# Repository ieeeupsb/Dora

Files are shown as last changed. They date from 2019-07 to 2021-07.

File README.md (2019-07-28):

View this project on [CADLAB.io](https://cadlab.io/project/1889). 

# Rasbot

## What is it?
This is a small differential terrestrial robot with all the sensors one can fit.
Its purpose is to have all the sensors and interfaces one can imagine so it can be used for research in various topics as well as different competitions.

Since its goal is to be resourceful in terms of sensing and actuating capabilities the design has expandability in mind. Therefore, there are a lot of exposed pins for modular expansions to the robot.

### Getting Support
There is extensive documentation on the Wiki page here on GitHub that covers the robot's design (hardware and software) as well as how to use this robot.

If you are a user of this robot and something is not working on your side please help us improve it. Open an issue here on GitHub!

### Contributing
Be it hardware or software, you can freely contribute to this project. Usually the Issues page here on GitHub has work that needs to be done. You are free to solve one yourself. Even if you are not familiar with hardware or software you can simply create new issues suggesting new things or changes/fixes to the current design.

This project is configured with CADLAB.io so visual differences of changes can be analysed.

If you are a contributor to this project keep in mind that pushing to the master branch is protected and can be only done by first creating a branch and then file a Pull Request which has to have at least two reviewers before it can be merged. This is meant to improve the quality of the project.

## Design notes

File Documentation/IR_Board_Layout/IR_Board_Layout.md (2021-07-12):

# Description

To do

# Size

To do

# To do

- [ ] Verify schematic
- [ ] Create basic layout figure
- [ ] Define board setup (track width, clearance, etc)
- [ ] Define board size
- [ ] Layout the board
- [ ] Check for possible issues with connections and sizes

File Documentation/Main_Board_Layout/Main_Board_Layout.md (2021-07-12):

# Description

## List of systems:
* Motors
  * Motor 1
  * Motor 2
  * Motor 3
  * Motor 4
  * Motor Encoders
* Power
  * 3.3V Buck
  * 5V Ultrasonic Buck
  * 5V RPi Buck
  * BMS
* MCU System
  * MCU
  * Power LED
  * Clock
  * EEPROM
  * Reset
  * Programming/Debugging
* IO System
  * RPi Headers
  * Expansion Headers
  * OLED
  * IMU
  * Buzzer
  * IR Array Module
  * RGB Leds
  * UltraSonic 1
  * UltraSonic 2
  * UltraSonic 3
  * UltraSonic 4

# Size

To do

# To do

- [ ] Verify schematic
- [ ] Create basic layout figure
- [ ] Define board setup (track width, clearance, etc)
- [ ] Define board size
- [ ] Layout the board
- [ ] Check for possible issues with connections and sizes

## Schematic
- [ ]  Jumpers SPI to IR board -> Add 100ohm (p.ex) resistance series to filter noise found on the connection wires (mainly in MISO, MOSI and CLK wires)
- [ ]  Check I2C1 and I2C2 resistors -> Normally 1-10k per device
- [ ]  Check bucks, mainly RPi 5v buck -> Vasco will check
- [ ]  Check dimensions of RPi to verify that it fits over the PCB
- [ ]  Check if IDC connector can handle 2.5A to RPi -> Vasco (Investigate the possibility of barrel jack RPi Power)

## Physical
- [ ]  Possibilities:
	* MicroRato: Dora Presentation (20cm×20cm  de  base  e  30cm  de altura)
		* Largura minima = Largura de motores + rodas
		* https://arxiv.org/pdf/1901.03638.pdf
	* Outro exemplo: 
		* https://developer.nvidia.com/embedded/diy-ai-race
		* https://www.myminifactory.com/object/3d-print-myrccar-1-10-mtc-chassis-rigid-axles-version-customizable-chassis-for-monster-crawler-or-scale-rc-car-79883	

# Some tips

## Layers
* Top layer -> Mixed
* In1 layer -> power plane (GND)
	*	Isolated GND planes for 3.3V, 5V and BAT with a small physical connection between them
* In2 layer -> power plane (VDD)
	* Isolated voltage planes
* Bot layer -> Mixed

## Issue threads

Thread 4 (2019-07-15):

Verify IR Matrix

G-Pereira, 2019-07-15:
Verify if the present IR Matrix schematic is correct.
The idea behind the current implementation is:
- One 9V rail powers each column completely to reduce components and power usage.
- Each column has its outputs multiplexed in order to read data row by row in parallel in order to reduce input pins to the number of rows.

However, this might not be optimal since 9V is too close to battery voltage and the battery can be lower than 9V during a normal discharge cycle. At the moment the plan is to use a buck-boost converter (acts as a buck while the battery is above 9V and as a boost while it's lower than that). Evaluate if it's needed to change this strategy.

G-Pereira, 2019-07-15:
Sadly there's no spice models for the CD4051B multiplexer

Closed 2019-07-22.

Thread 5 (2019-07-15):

Motor Driver

G-Pereira, 2019-07-15:
For the motors we already have (ask for the voltage rating) design the motor driver circuit and define its power draw at max output power.
It's useful to have a current limiting architecture here. There are several ways to do this, ask in Slack if you are lost.

Closed 2019-08-21.

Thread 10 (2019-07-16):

connect IMU system

G-Pereira, 2019-07-16:
Connect gyroscope and compass to the I2C bus and if needed set their configuration pins.

G-Pereira, 2019-08-05:
Sorry to change this even tho the schematic is already settled but BMX055 is the same as BNO055 without the ARM microcontroller built-in. This means changing to BMX055 gives access to raw sensor data and a considerably price drop.

Closed 2021-03-10.

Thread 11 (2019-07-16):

Design connection from Raspberry Pi to MCU

G-Pereira, 2019-07-16:
Maybe just one UART connection is needed but take some time to think what interfaces are useful and what the Raspberry could be able to do. Then, design a schematic for that

Closed 2019-09-09.

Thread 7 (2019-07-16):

Design RF Receiver

G-Pereira, 2019-07-16:
~~Design a RF Receiver decoder to read a RF433 module in order to design a remote control later on.
The idea is to expose a Dupont connector to plug in a receiver but it's necessary to deserialize the data that comes from it.
First 8 bits are address and the next 4 are data so in other to offload address verification the use of HT12D is highly recommended. The MCU would have to constantly read all RF signals and evaluate if it's our remote talking. This way the MCU receives from HT12D's VT pin (connected to an interruption enabled pin) a signal that our remote has sent data and then the data pins can be read in order to read the command sent through.~~

~~An NRF24 make the process esier, is more reliable, faster, supports longer distance and it's way cheaper. A more reputable brand (Nordic Semiconductor) manufactures them.
Design a connector for it. It uses SPI~~

Design a LoRa interface

Closed 2019-08-26.

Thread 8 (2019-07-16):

LCD Screen Menu Interface

G-Pereira, 2019-07-16:
In other to change robot's parameters or function and display battery status, design a connector for a SSD1306 LCD. Include a clickable rotary encoder in order to navigate menu. Plan the connections to the MCU.

Closed 2019-07-28.

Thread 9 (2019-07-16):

Read Motor Encoders

G-Pereira, 2019-07-16:
Our motors include two magnetic sensors to read motors rotation. Plan the connection of this 4 pins (2 for each motor). Evaluate if more than direct connection is possible. These pins if connected to an interrupt pin can generate a high rate of interrupt calls and that will require a high frequency clock MCU which can be avoided. Design a hardware solution for this.

Closed 2019-07-28.

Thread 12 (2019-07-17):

Ultrassonic Sensors connectors

G-Pereira, 2019-07-17:
Design a connection for sonars (dupont). Each one consists of 4 pins:
- Power (VCC and GND)
- Trig - Sensor input to begin reading process (Generic MCU I/O)
- Echo - sensor output signal (Generic MCU I/O)
There will be 4 of them

Closed 2019-07-28.

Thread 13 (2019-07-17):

Battery Level Sensor

G-Pereira, 2019-07-17:
Design hardware to read efficiently the battery status (there's ICs in the market for this).
Make sure the solution is appropriate for LiPo batteries.
Battery will be a LiPo 3C 11.1V

Sleepy105, 2019-07-22:
https://www.digikey.com/product-detail/en/texas-instruments/BQ76925PWR/296-29341-1-ND/2728027

JoaoGarrido, 2019-07-29:
Datasheet:
http://www.ti.com/lit/ds/symlink/bq76925.pdf
Application notes:
http://www.ti.com/lit/an/slua707/slua707.pdf

Some notes:
- LDO regulator from the IC will not power the MCU(what should i do with it?)
- Not sure how to do the battery temperature part

Closed 2021-03-10.

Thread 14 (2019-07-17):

Add debug interfaces (visual or audible)

G-Pereira, 2019-07-17:
Add 1 buzzer and 3 RGB LED to help debug applications and to show various status like battery's status.
Use PWM for both buzzer and RGB LEDs.
Add more if you find it useful

G-Pereira, 2019-07-22:
1K resistor fits both interfaces and minimizes power usage.

Closed 2019-07-28.

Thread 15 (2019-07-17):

Design Buck Converters

G-Pereira, 2019-07-17:
This should be only done at the end of the schematic where the circuit is well defined in terms of power draw.
From the time of this writing it is being planned to have various voltage levels. Use a Texas Instruments device for this since there's experience with these ICs.

Closed 2019-08-26.

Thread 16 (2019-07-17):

Early pick of MCU

G-Pereira, 2019-07-17:
At this stage pick a STM32 family of devices by looking at their top level features and pick one with a decent amount of pins to begin planning MCU connections. Don't waste time thinking on the number of I/O in detail.
On the final stages of development the MCU will be revised and sized.
Only make sure to set STM32 family on stone (this is important) in order to avoid wasting time.

Sleepy105, 2019-07-22:
STM32F4 family

Closed 2019-07-22.

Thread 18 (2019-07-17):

Design add-on connector

G-Pereira, 2019-07-17:
Design a connector for future improvements of the robot.
Be sure to expose everything it can be used. Don't forget to expose I2C and SPI bus even if that's in use because it can be added more devices to those buses.

Closed 2021-03-10.

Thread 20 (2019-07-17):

Design PCB

G-Pereira, 2019-07-17:
Layout components on the PCB. @G-Pereira will be definitively involved in this but be free to assign yourself also to this issue if you would like to help.

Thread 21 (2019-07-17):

Design CAD Model of Enclosure

G-Pereira, 2019-07-17:
Design an enclosure that fits a 100x100mm PCB. The fixings can be anywhere, just inform Electrical team where you plan to have screws or other types of fixings.

pedro-brands, 2019-07-17:
Portanto, eu vou fazer o design estrutural e o outro Pedro vai servir de consultor.

G-Pereira, 2019-07-18:
Ok, porreiro. nós vamos ter duas PCBs, uma mais junto ao chão com sensores de linha e outra principal. a ideia é fazer o robô o mais pequeno possivel e a PCB vai ter um máximo de 100x100mm (pode vir a ser mais pequena). Temos dois motores já no núcleo, as dimensões vão ser publicadas aqui #22 e por fim, temos de colocar vários LEDs (na verdade são sensores) a apontar para todas as direções (por volta de 12 LEDs) a uma altura razoável, por isso é preciso planear uma espécie de torre também. Tudo claro?

pedro-brands, 2019-07-18:
Muito bem, percebido! O luis já me tinha dado algumas indicações! Amanhã começo a fazer drafts de como pode ser o modelo e depois coloco aqui

G-Pereira, 2019-07-19:
Porreiro!

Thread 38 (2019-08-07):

Computer mouse sensor

G-Pereira, 2019-08-07:
Use an off-the-shelf computer mouse tracking sensor to improve the odometry of the robot. This should be designed as a plugin since it will be detached from the mainboard. This sensor, as you know, has to be really close to the ground almost dragging. Discuss with MCAD team if this is feasible.

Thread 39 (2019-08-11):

Add EEPROM

G-Pereira, 2019-08-11:
High performance STM32 MCU doesn't feature an EEPROM. This can be useful for configurations. Pick one EEPROM chip and design a circuit to connect it to the MCU

G-Pereira, 2019-08-12:
24LC256 was picked

Closed 2019-08-14.

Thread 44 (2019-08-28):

Design HouseKeeping circuit

G-Pereira, 2019-08-28:
Design a microcontroller circuit that is responsible for the safe functioning of the device that is responsible for safe shutdown of raspberry pi, power on/off power rails and subcircuits. This microcontroller will be alway connected to the battery so it should be a STM32L series to get power consumption of around 50uA. Because of this the external power switch will be a soft shutdown so a not so accessible (so people don't use it) power switch should be integrated because even with low current draw, after months the battery could be wasted.

G-Pereira, 2019-09-07:
Not really important

Closed 2019-09-07.

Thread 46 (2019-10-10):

Level Shifters Sonar

G-Pereira, 2019-10-10:
Sonar Echo pins need to be shifted to 3.3V logic with AO3400

morallito, 2019-10-19:
Implementado no branch BMS commit "3.3 - 5V level shifter sonar with 2n3904

morallito, 2019-10-19:
@G-Pereira confira se é isto que querias!

Closed 2019-10-25.

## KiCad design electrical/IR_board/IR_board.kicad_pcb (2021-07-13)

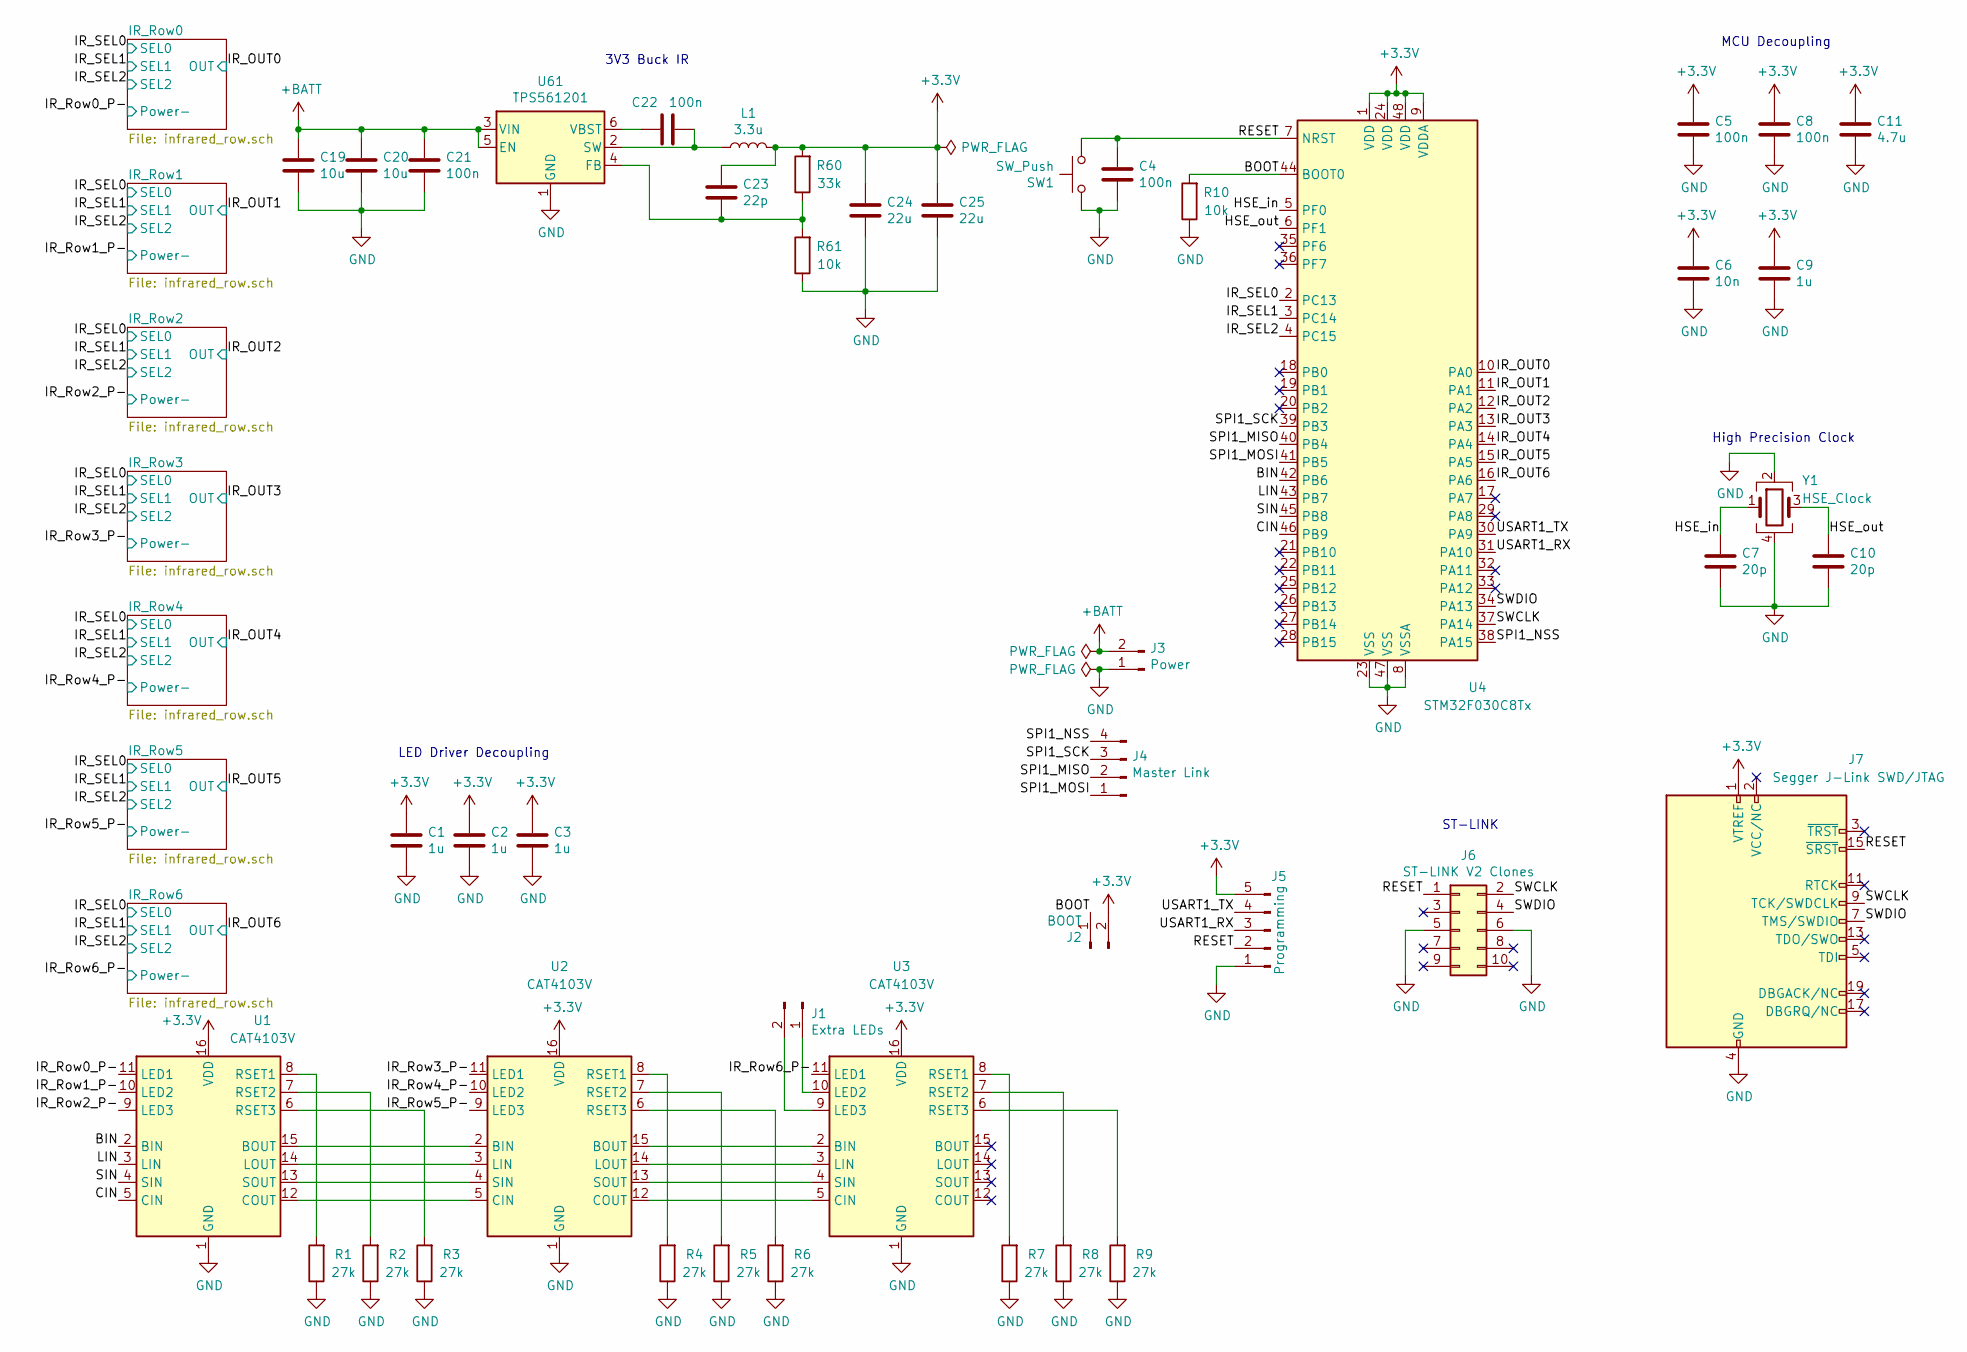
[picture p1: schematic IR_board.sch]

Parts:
C1, C2, C3, C9: 1u; C_0603_1608Metric
C4, C5, C8: 100n; C_0603_1608Metric
C6: 10n; C_0603_1608Metric
C7, C10: 20p; C_0603_1608Metric
C11: 4.7u; C_0603_1608Metric
C19, C20: 10u; C_1206_3216Metric
C21, C22: 100n; C_1206_3216Metric
C23: 22p; C_0603_1608Metric
C24, C25: 22u; C_0603_1608Metric
J1: Extra LEDs; PinHeader_1x02_P2.54mm_Horizontal
J2: BOOT; PinHeader_1x02_P2.54mm_Horizontal
J3: Power; JST_XH_S2B-XH-A-1_1x02_P2.50mm_Horizontal
J4: Master Link; JST_XH_S4B-XH-A-1_1x04_P2.50mm_Horizontal
J5: Programming; PinHeader_1x05_P2.54mm_Horizontal
J6: ST-LINK V2 Clones; IDC-Header_2x05_P2.54mm_Vertical
J7: Segger J-Link SWD/JTAG; IDC-Header_2x10_P2.54mm_Vertical
L1: 3.3u; L_Coilcraft_LPS4018
R1, R2, R3, R4, R5, R6, R7, R8, R9: 27k; R_0603_1608Metric
R10, R61: 10k; R_0603_1608Metric
R60: 33k; R_0603_1608Metric
SW1: SW_Push; SW_PUSH_6mm
U1, U2, U3: CAT4103V; SOIC-16_3.9x9.9mm_P1.27mm
U4: STM32F030C8Tx; LQFP-48_7x7mm_P0.5mm
U61: TPS561201; SOT-23-8
Y1: HSE_Clock; Crystal_SMD_5032-4Pin_5.0x3.2mm

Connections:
+3V3: C1.1, C2.1, C3.1, C5.1, C6.1, C8.1, C9.1, C11.1, C23.1, C24.1, C25.1, J2.2, J5.5, J7.1 (VTREF), L1.2, R60.2, U1.16 (VDD), U2.16 (VDD), U3.16 (VDD), U4.1 (VDD), U4.9 (VDDA), U4.24 (VDD), U4.48 (VDD); also elsewhere on the board
+BATT: C19.1, C20.1, C21.1, J3.2, U61.3 (VIN), U61.5 (EN); also elsewhere on the board
/BIN: U1.2 (BIN), U4.42 (PB6)
/BOOT: J2.1, R10.2, U4.44 (BOOT0)
/CIN: U1.5 (CIN), U4.46 (PB9)
/HSE_in: C7.1, U4.5 (PF0), Y1.1
/HSE_out: C10.1, U4.6 (PF1), Y1.3
/IR_OUT0: U4.10 (PA0); also elsewhere on the board
/IR_OUT1: U4.11 (PA1); also elsewhere on the board
/IR_OUT2: U4.12 (PA2); also elsewhere on the board
/IR_OUT3: U4.13 (PA3); also elsewhere on the board
/IR_OUT4: U4.14 (PA4); also elsewhere on the board
/IR_OUT5: U4.15 (PA5); also elsewhere on the board
/IR_OUT6: U4.16 (PA6); also elsewhere on the board
/IR_Row0_P-: U1.11 (LED1); also elsewhere on the board
/IR_Row1_P-: U1.10 (LED2); also elsewhere on the board
/IR_Row2_P-: U1.9 (LED3); also elsewhere on the board
/IR_Row3_P-: U2.11 (LED1); also elsewhere on the board
/IR_Row4_P-: U2.10 (LED2); also elsewhere on the board
/IR_Row5_P-: U2.9 (LED3); also elsewhere on the board
/IR_Row6_P-: U3.11 (LED1); also elsewhere on the board
/IR_SEL0: U4.2 (PC13); also elsewhere on the board
/IR_SEL1: U4.3 (PC14); also elsewhere on the board
/IR_SEL2: U4.4 (PC15); also elsewhere on the board
/LIN: U1.3 (LIN), U4.43 (PB7)
/RESET: C4.1, J5.2, J6.1, J7.15 (~SRST~), SW1.2, U4.7 (NRST)
/SIN: U1.4 (SIN), U4.45 (PB8)
/SPI1_MISO: J4.2, U4.40 (PB4)
/SPI1_MOSI: J4.1, U4.41 (PB5)
/SPI1_NSS: J4.4, U4.38 (PA15)
/SPI1_SCK: J4.3, U4.39 (PB3)
/SWCLK: J6.2, J7.9 (TCK/SWDCLK), U4.37 (PA14)
/SWDIO: J6.4, J7.7 (TMS/SWDIO), U4.34 (PA13)
/USART1_RX: J5.3, U4.31 (PA10)
/USART1_TX: J5.4, U4.30 (PA9)
GND: C1.2, C2.2, C3.2, C4.2, C5.2, C6.2, C7.2, C8.2, C9.2, C10.2, C11.2, C19.2, C20.2, C21.2, C24.2, C25.2, J3.1, J5.1, J6.5, J6.6, J7.4 (GND), J7.6 (GND), J7.8 (GND), J7.10 (GND), J7.12 (GND), J7.14 (GND), J7.16 (GND), J7.18 (GND), J7.20 (GND), R1.1, R2.1, R3.1, R4.1, R5.1, R6.1, R7.1, R8.1, R9.1, R10.1, R61.1, SW1.1, U1.1 (GND), U2.1 (GND), U3.1 (GND), U4.8 (VSSA), U4.23 (VSS), U4.47 (VSS), U61.1 (GND), Y1.2, Y1.4; also elsewhere on the board
unnamed: C22.1, U61.6 (VBST)
unnamed: C22.2, L1.1, U61.2 (SW)
unnamed: C23.2, R60.1, R61.2, U61.4 (FB)
unnamed: J1.1, U3.10 (LED2)
unnamed: J1.2, U3.9 (LED3)
unnamed: R1.2, U1.8 (RSET1)
unnamed: R2.2, U1.7 (RSET2)
unnamed: R3.2, U1.6 (RSET3)
unnamed: R4.2, U2.8 (RSET1)
unnamed: R5.2, U2.7 (RSET2)
unnamed: R6.2, U2.6 (RSET3)
unnamed: R7.2, U3.8 (RSET1)
unnamed: R8.2, U3.7 (RSET2)
unnamed: R9.2, U3.6 (RSET3)
unnamed: U1.12 (COUT), U2.5 (CIN)
unnamed: U1.13 (SOUT), U2.4 (SIN)
unnamed: U1.14 (LOUT), U2.3 (LIN)
unnamed: U1.15 (BOUT), U2.2 (BIN)
unnamed: U2.12 (COUT), U3.5 (CIN)
unnamed: U2.13 (SOUT), U3.4 (SIN)
unnamed: U2.14 (LOUT), U3.3 (LIN)
unnamed: U2.15 (BOUT), U3.2 (BIN)

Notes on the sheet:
LED Driver Decoupling
ST-LINK
High Precision Clock
MCU Decoupling
3V3 Buck IR

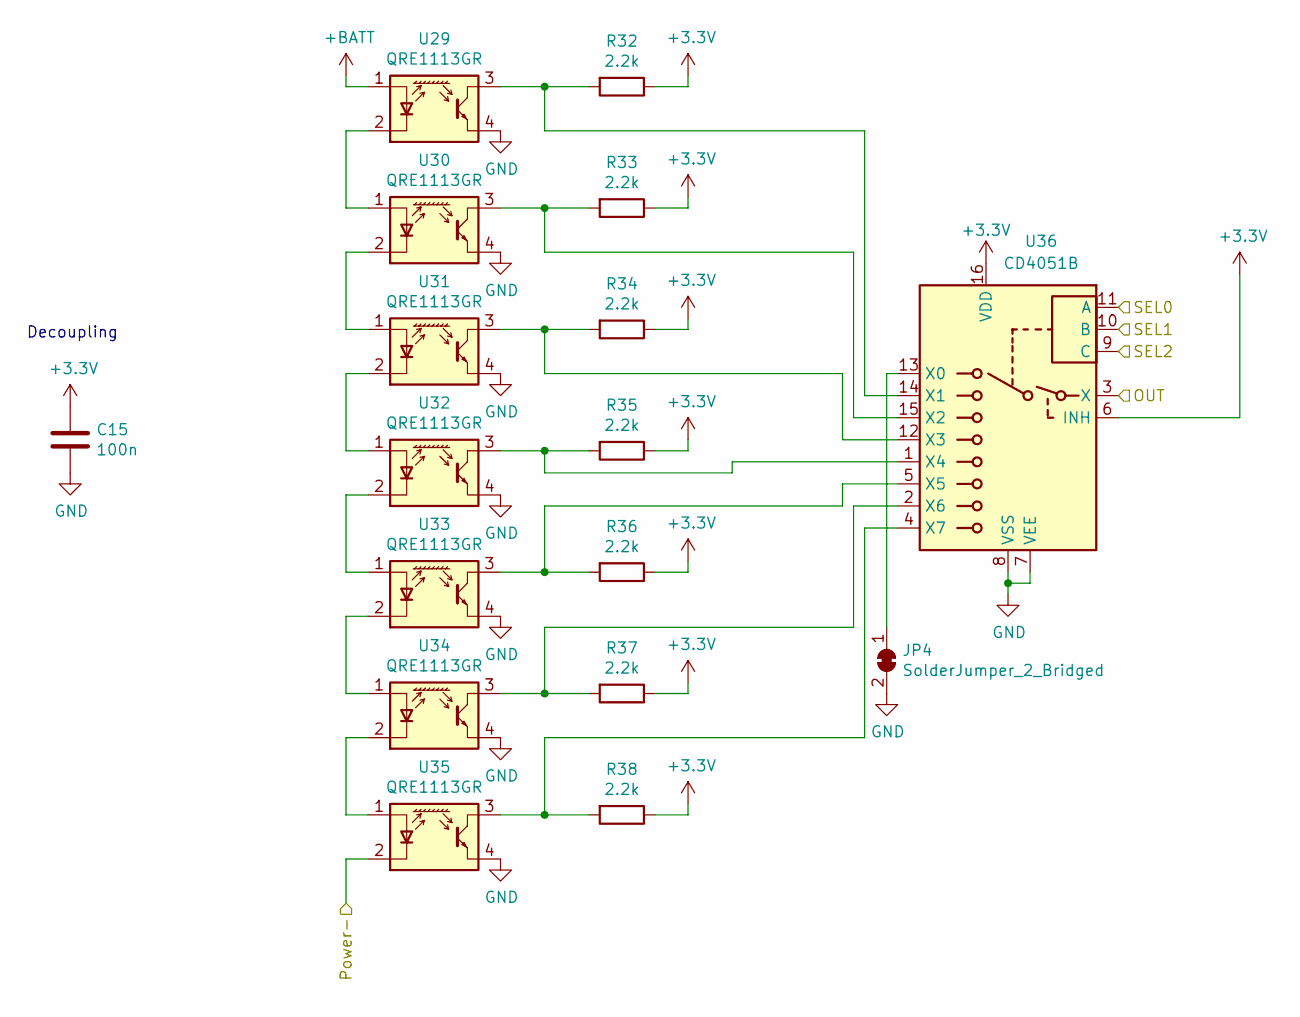
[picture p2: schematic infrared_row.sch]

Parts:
C17: 100n; C_0603_1608Metric
JP4: SolderJumper_2_Bridged; SolderJumper-2_P1.3mm_Bridged_Pad1.0x1.5mm
R46, R47, R48, R49, R50, R51, R52: 2.2k; R_0603_1608Metric
U45, U46, U47, U48, U49, U50, U51: QRE1113GR; OnSemi_CASE100CY
U52: CD4051B; SOP-16_4.55x10.3mm_P1.27mm

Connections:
+3V3: C17.1, R46.1, R47.1, R48.1, R49.1, R50.1, R51.1, R52.1, U52.6 (INH), U52.16 (VDD); also elsewhere on the board
+BATT: U45.1 (A); also elsewhere on the board
/IR_OUT6: U52.3 (X); also elsewhere on the board
/IR_Row6_P-: U51.2 (K); also elsewhere on the board
/IR_SEL0: U52.11 (A); also elsewhere on the board
/IR_SEL1: U52.10 (B); also elsewhere on the board
/IR_SEL2: U52.9 (C); also elsewhere on the board
GND: C17.2, JP4.2 (B), U45.4, U46.4, U47.4, U48.4, U49.4, U50.4, U51.4, U52.7 (VEE), U52.8 (VSS); also elsewhere on the board
unnamed: R46.2, U45.3, U52.14 (X1)
unnamed: R47.2, U46.3, U52.15 (X2)
unnamed: R48.2, U47.3, U52.12 (X3)
unnamed: R49.2, U48.3, U52.1 (X4)
unnamed: R50.2, U49.3, U52.5 (X5)
unnamed: R51.2, U50.3, U52.2 (X6)
unnamed: R52.2, U51.3, U52.4 (X7)
unnamed: U45.2 (K), U46.1 (A)
unnamed: U46.2 (K), U47.1 (A)
unnamed: U47.2 (K), U48.1 (A)
unnamed: U48.2 (K), U49.1 (A)
unnamed: U49.2 (K), U50.1 (A)
unnamed: U50.2 (K), U51.1 (A)

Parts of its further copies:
C12, C13, C14, C15, C16, C18: 100n; C_0603_1608Metric
JP1, JP2, JP3, JP5, JP6, JP7: SolderJumper_2_Bridged; SolderJumper-2_P1.3mm_Bridged_Pad1.0x1.5mm
R11, R12, R13, R14, R15, R16, R17, R18, R19, R20, R21, R22, R23, R24, R25, R26, R27, R28, R29, R30, R31, R32, R33, R34, R35, R36, R37, R38, R39, R40, R41, R42, R43, R44, R45, R53, R54, R55, R56, R57, R58, R59: 2.2k; R_0603_1608Metric
U5, U6, U7, U8, U9, U10, U11, U13, U14, U15, U16, U17, U18, U19, U21, U22, U23, U24, U25, U26, U27, U29, U30, U31, U32, U33, U34, U35, U37, U38, U39, U40, U41, U42, U43, U53, U54, U55, U56, U57, U58, U59: QRE1113GR; OnSemi_CASE100CY
U12, U20, U28, U36, U44, U60: CD4051B; SOP-16_4.55x10.3mm_P1.27mm

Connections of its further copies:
+3V3: C12.1, C13.1, C14.1, C15.1, C16.1, C18.1, R11.1, R12.1, R13.1, R14.1, R15.1, R16.1, R17.1, R18.1, R19.1, R20.1, R21.1, R22.1, R23.1, R24.1, R25.1, R26.1, R27.1, R28.1, R29.1, R30.1, R31.1, R32.1, R33.1, R34.1, R35.1, R36.1, R37.1, R38.1, R39.1, R40.1, R41.1, R42.1, R43.1, R44.1, R45.1, R53.1, R54.1, R55.1, R56.1, R57.1, R58.1, R59.1, U12.6 (INH), U12.16 (VDD), U20.6 (INH), U20.16 (VDD), U28.6 (INH), U28.16 (VDD), U36.6 (INH), U36.16 (VDD), U44.6 (INH), U44.16 (VDD), U60.6 (INH), U60.16 (VDD); also elsewhere on the board
+BATT: U5.1 (A), U13.1 (A), U21.1 (A), U29.1 (A), U37.1 (A), U53.1 (A); also elsewhere on the board
/IR_OUT0: U60.3 (X); also elsewhere on the board
/IR_OUT1: U12.3 (X); also elsewhere on the board
/IR_OUT2: U44.3 (X); also elsewhere on the board
/IR_OUT3: U20.3 (X); also elsewhere on the board
/IR_OUT4: U28.3 (X); also elsewhere on the board
/IR_OUT5: U36.3 (X); also elsewhere on the board
/IR_Row0_P-: U59.2 (K); also elsewhere on the board
/IR_Row1_P-: U11.2 (K); also elsewhere on the board
/IR_Row2_P-: U43.2 (K); also elsewhere on the board
/IR_Row3_P-: U19.2 (K); also elsewhere on the board
/IR_Row4_P-: U27.2 (K); also elsewhere on the board
/IR_Row5_P-: U35.2 (K); also elsewhere on the board
/IR_SEL0: U12.11 (A), U20.11 (A), U28.11 (A), U36.11 (A), U44.11 (A), U60.11 (A); also elsewhere on the board
/IR_SEL1: U12.10 (B), U20.10 (B), U28.10 (B), U36.10 (B), U44.10 (B), U60.10 (B); also elsewhere on the board
/IR_SEL2: U12.9 (C), U20.9 (C), U28.9 (C), U36.9 (C), U44.9 (C), U60.9 (C); also elsewhere on the board
GND: C12.2, C13.2, C14.2, C15.2, C16.2, C18.2, JP1.2 (B), JP2.2 (B), JP3.2 (B), JP5.2 (B), JP6.2 (B), JP7.2 (B), U5.4, U6.4, U7.4, U8.4, U9.4, U10.4, U11.4, U12.7 (VEE), U12.8 (VSS), U13.4, U14.4, U15.4, U16.4, U17.4, U18.4, U19.4, U20.7 (VEE), U20.8 (VSS), U21.4, U22.4, U23.4, U24.4, U25.4, U26.4, U27.4, U28.7 (VEE), U28.8 (VSS), U29.4, U30.4, U31.4, U32.4, U33.4, U34.4, U35.4, U36.7 (VEE), U36.8 (VSS), U37.4, U38.4, U39.4, U40.4, U41.4, U42.4, U43.4, U44.7 (VEE), U44.8 (VSS), U53.4, U54.4, U55.4, U56.4, U57.4, U58.4, U59.4, U60.7 (VEE), U60.8 (VSS); also elsewhere on the board
unnamed: JP1.1 (A), U12.13 (X0)
unnamed: JP2.1 (A), U20.13 (X0)
unnamed: JP3.1 (A), U28.13 (X0)
unnamed: JP5.1 (A), U44.13 (X0)
unnamed: JP7.1 (A), U60.13 (X0)
unnamed: R11.2, U5.3, U12.14 (X1)
unnamed: R12.2, U6.3, U12.15 (X2)
unnamed: R13.2, U7.3, U12.12 (X3)
unnamed: R14.2, U8.3, U12.1 (X4)
unnamed: R15.2, U9.3, U12.5 (X5)
unnamed: R16.2, U10.3, U12.2 (X6)
unnamed: R17.2, U11.3, U12.4 (X7)
unnamed: R18.2, U13.3, U20.14 (X1)
unnamed: R19.2, U14.3, U20.15 (X2)
unnamed: R20.2, U15.3, U20.12 (X3)
unnamed: R21.2, U16.3, U20.1 (X4)
unnamed: R22.2, U17.3, U20.5 (X5)
unnamed: R23.2, U18.3, U20.2 (X6)
unnamed: R24.2, U19.3, U20.4 (X7)
unnamed: R25.2, U21.3, U28.14 (X1)
unnamed: R26.2, U22.3, U28.15 (X2)
unnamed: R27.2, U23.3, U28.12 (X3)
unnamed: R28.2, U24.3, U28.1 (X4)
unnamed: R29.2, U25.3, U28.5 (X5)
unnamed: R30.2, U26.3, U28.2 (X6)
unnamed: R31.2, U27.3, U28.4 (X7)
unnamed: R32.2, U29.3, U36.14 (X1)
unnamed: R33.2, U30.3, U36.15 (X2)
unnamed: R34.2, U31.3, U36.12 (X3)
unnamed: R35.2, U32.3, U36.1 (X4)
unnamed: R36.2, U33.3, U36.5 (X5)
unnamed: R37.2, U34.3, U36.2 (X6)
unnamed: R38.2, U35.3, U36.4 (X7)
unnamed: R39.2, U37.3, U44.14 (X1)
unnamed: R40.2, U38.3, U44.15 (X2)
unnamed: R41.2, U39.3, U44.12 (X3)
unnamed: R42.2, U40.3, U44.1 (X4)
unnamed: R43.2, U41.3, U44.5 (X5)
unnamed: R44.2, U42.3, U44.2 (X6)
unnamed: R45.2, U43.3, U44.4 (X7)
unnamed: R53.2, U53.3, U60.14 (X1)
unnamed: R54.2, U54.3, U60.15 (X2)
unnamed: R55.2, U55.3, U60.12 (X3)
unnamed: R56.2, U56.3, U60.1 (X4)
unnamed: R57.2, U57.3, U60.5 (X5)
unnamed: R58.2, U58.3, U60.2 (X6)
unnamed: R59.2, U59.3, U60.4 (X7)
unnamed: U5.2 (K), U6.1 (A)
unnamed: U6.2 (K), U7.1 (A)
unnamed: U7.2 (K), U8.1 (A)
unnamed: U8.2 (K), U9.1 (A)
unnamed: U9.2 (K), U10.1 (A)
unnamed: U10.2 (K), U11.1 (A)
unnamed: U13.2 (K), U14.1 (A)
unnamed: U14.2 (K), U15.1 (A)
unnamed: U15.2 (K), U16.1 (A)
unnamed: U16.2 (K), U17.1 (A)
unnamed: U17.2 (K), U18.1 (A)
unnamed: U18.2 (K), U19.1 (A)
unnamed: U21.2 (K), U22.1 (A)
unnamed: U22.2 (K), U23.1 (A)
unnamed: U23.2 (K), U24.1 (A)
unnamed: U24.2 (K), U25.1 (A)
unnamed: U25.2 (K), U26.1 (A)
unnamed: U26.2 (K), U27.1 (A)
unnamed: U29.2 (K), U30.1 (A)
unnamed: U30.2 (K), U31.1 (A)
unnamed: U31.2 (K), U32.1 (A)
unnamed: U32.2 (K), U33.1 (A)
unnamed: U33.2 (K), U34.1 (A)
unnamed: U34.2 (K), U35.1 (A)
unnamed: U37.2 (K), U38.1 (A)
unnamed: U38.2 (K), U39.1 (A)
unnamed: U39.2 (K), U40.1 (A)
unnamed: U40.2 (K), U41.1 (A)
unnamed: U41.2 (K), U42.1 (A)
unnamed: U42.2 (K), U43.1 (A)
unnamed: U53.2 (K), U54.1 (A)
unnamed: U54.2 (K), U55.1 (A)
unnamed: U55.2 (K), U56.1 (A)
unnamed: U56.2 (K), U57.1 (A)
unnamed: U57.2 (K), U58.1 (A)
unnamed: U58.2 (K), U59.1 (A)

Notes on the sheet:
Decoupling

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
Board: 2 copper layers, 164 parts (0 on the bottom side), 156 nets, no tracks yet.

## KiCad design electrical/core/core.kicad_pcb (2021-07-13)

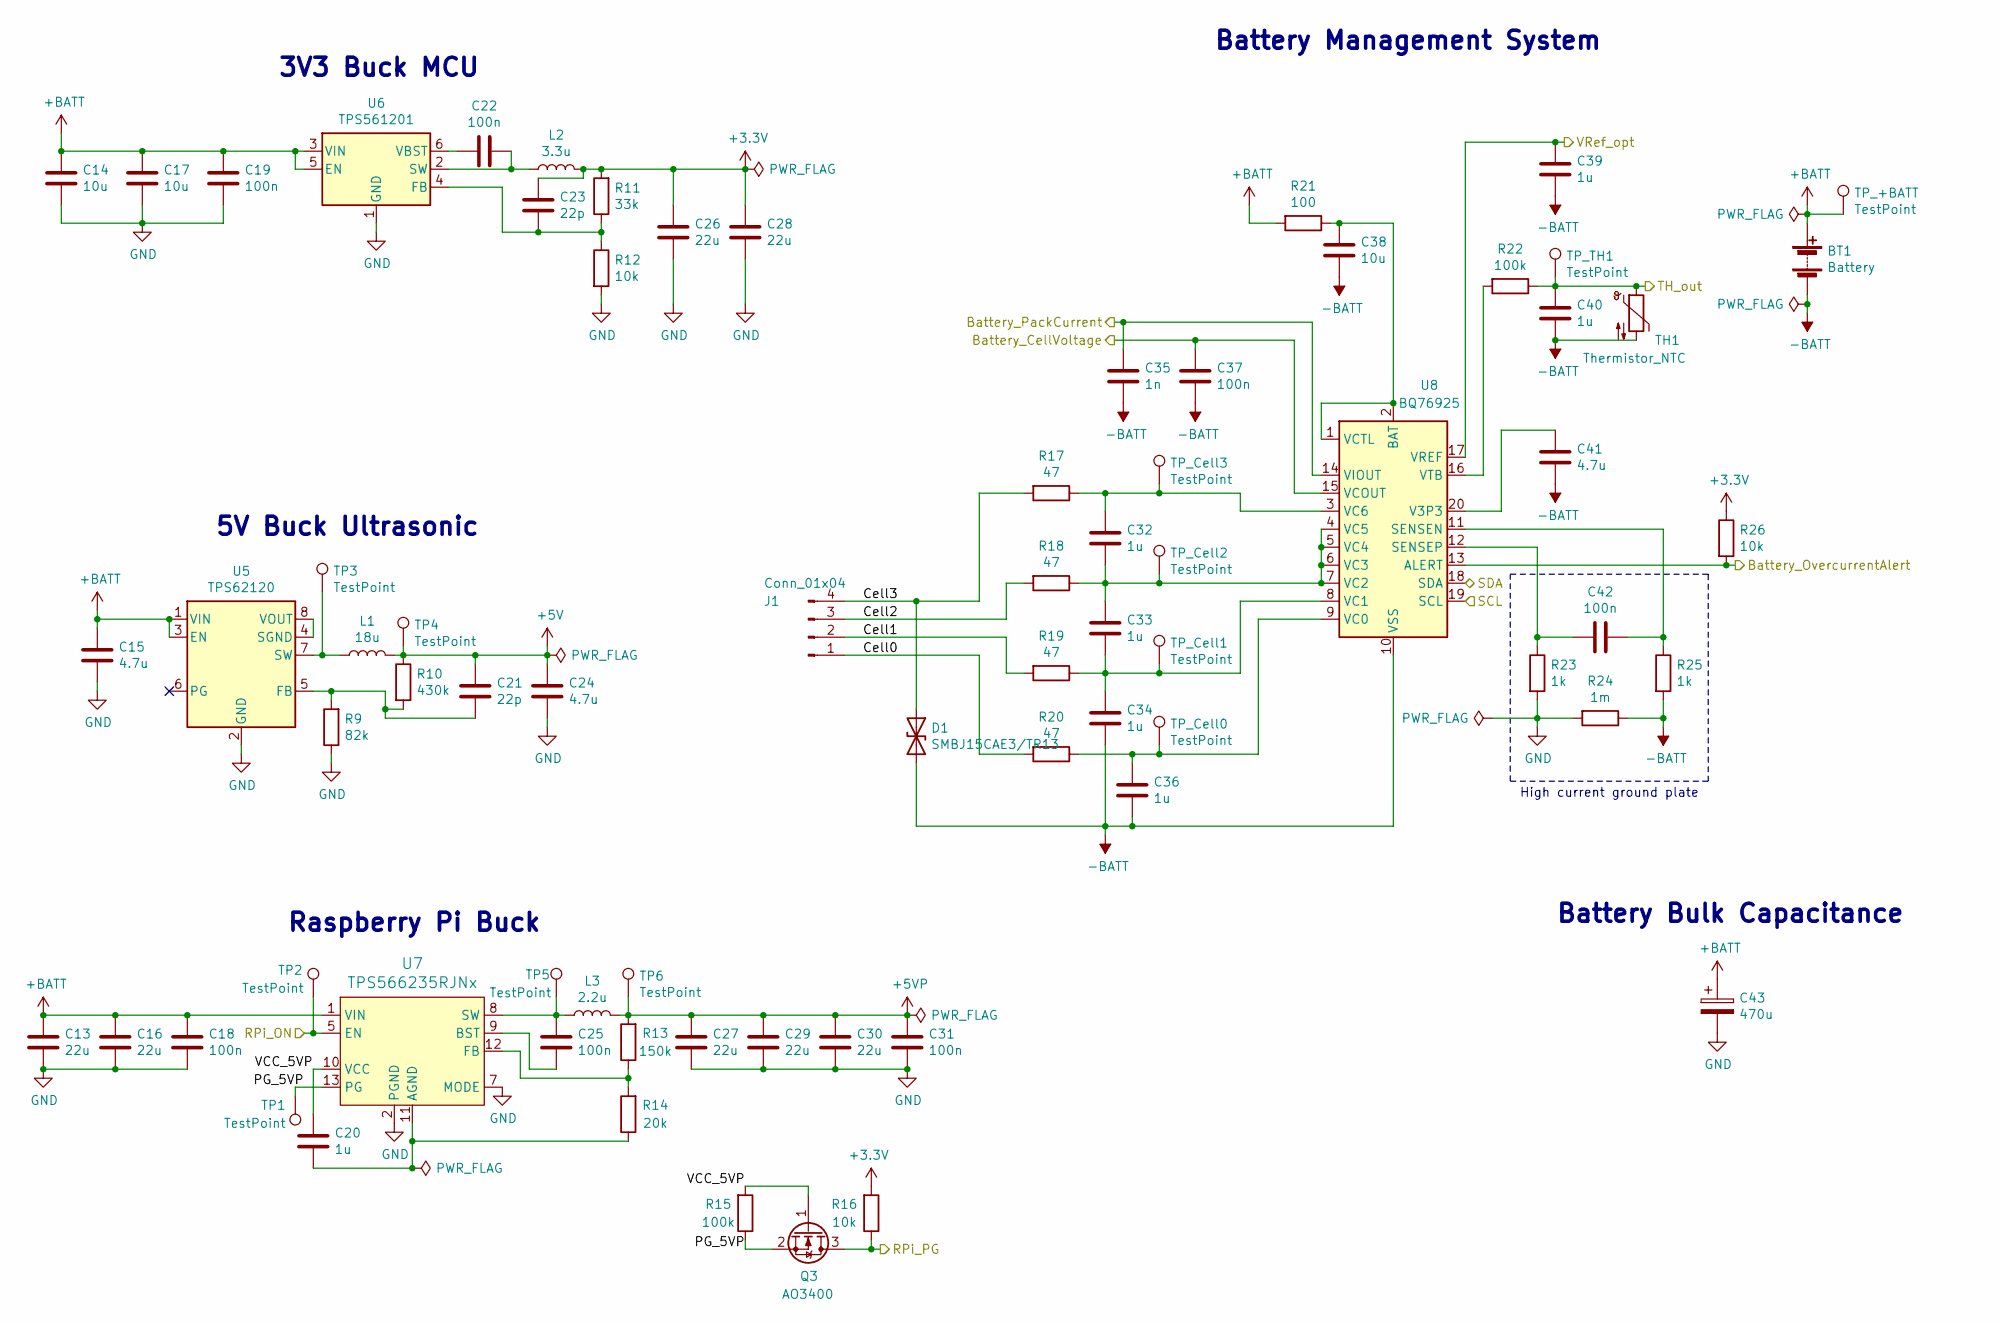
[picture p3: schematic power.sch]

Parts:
BT1: Battery; SolderWire-2.5sqmm_1x02_P7.2mm_D2.4mm_OD3.6mm_Relief_12AWG_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
C13, C16: 22u; C_1206_3216Metric
C14, C17, C38: 10u; C_1206_3216Metric
C15: 4.7u; C_1206_3216Metric
C18, C19, C22, C25, C42: 100n; C_1206_3216Metric
C20, C32, C33, C34, C36, C39, C40: 1u; C_0603_1608Metric
C21, C23: 22p; C_0603_1608Metric
C24, C41: 4.7u; C_0603_1608Metric
C26, C27, C28, C29, C30: 22u; C_0603_1608Metric
C31, C37: 100n; C_0603_1608Metric
C35: 1n; C_0603_1608Metric
C43: 470u; CP_Elec_10x10
D1: SMBJ15CAE3/TR13; D_SMB
J1: Conn_01x04; JST_XH_S4B-XH-A-1_1x04_P2.50mm_Horizontal
L1: 18u; L_Coilcraft_LPS4018
L2: 3.3u; L_Coilcraft_LPS4018
L3: 2.2u; L_10.4x10.4_H4.8
Q3: AO3400; SOT-23
R9: 82k; R_0603_1608Metric
R10: 430k; R_0603_1608Metric
R11: 33k; R_0603_1608Metric
R12, R16, R26: 10k; R_0603_1608Metric
R13: 150k; R_0603_1608Metric
R14: 20k; R_0603_1608Metric
R15, R22: 100k; R_0603_1608Metric
R17, R18, R19, R20: 47; R_0603_1608Metric
R21: 100; R_0603_1608Metric
R23, R25: 1k; R_0603_1608Metric
R24: 1m; R_2512_6332Metric
TH1: Thermistor_NTC; PinHeader_1x02_P2.54mm_Horizontal
TP1, TP2, TP3, TP4, TP5, TP6: TestPoint; TestPoint_Pad_D1.0mm
TP_+BATT: TestPoint; TestPoint_Pad_D1.0mm
TP_Cell0, TP_Cell1, TP_Cell2, TP_Cell3: TestPoint; TestPoint_Pad_D1.0mm
TP_TH1: TestPoint; TestPoint_Pad_D1.0mm
U5: TPS62120; SOT-23-8
U6: TPS561201; SOT-23-8
U7: TPS566235RJNx; VQFN-13-1EP_3x3mm_P0.5mm_EP1.6x1.6mm
U8: BQ76925; TSSOP-20_4.4x6.5mm_P0.65mm

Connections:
+3V3: C23.1, C26.1, C28.1, L2.2, R11.2, R16.2, R26.1; also elsewhere on the board
+5V: C21.1, C24.1, L1.2, R10.1, TP4.1; also elsewhere on the board
+5VP: C27.1, C29.1, C30.1, C31.1, L3.2, R13.2, TP6.1; also elsewhere on the board
+BATT: BT1.1 (+), C13.1, C14.1, C15.1, C16.1, C17.1, C18.1, C19.1, C43.1, R21.2, TP_+BATT.1, U5.1 (VIN), U5.3 (EN), U6.3 (VIN), U6.5 (EN), U7.1 (VIN); also elsewhere on the board
-BATT: BT1.2 (-), C34.2, C35.2, C36.2, C37.2, C38.2, C39.2, C40.2, C41.2, D1.2 (A2), R24.1, R25.2, TH1.2, U8.10 (VSS)
/Battery_Cell_Voltage: C37.1, U8.15 (VCOUT); also elsewhere on the board
/Battery_Current: C35.1, U8.14 (VIOUT); also elsewhere on the board
/Battery_Overcurrent: R26.2, U8.13 (ALERT); also elsewhere on the board
/Battery_Temperature: C40.1, R22.1, TH1.1, TP_TH1.1; also elsewhere on the board
/I2C1_SCL: U8.19 (SCL); also elsewhere on the board
/I2C1_SDA: U8.18 (SDA); also elsewhere on the board
/Power/Cell0: J1.1, R20.2
/Power/Cell1: J1.2, R19.2
/Power/Cell2: J1.3, R18.2
/Power/Cell3: D1.1 (A1), J1.4, R17.2
/Power/PG_5VP: Q3.2 (S), R15.1, TP1.1, U7.13 (PG)
/Power/VCC_5VP: C20.1, Q3.1 (G), R15.2, U7.10 (VCC)
/RPi_EN: TP2.1, U7.5 (EN); also elsewhere on the board
/RPi_PG: Q3.3 (D), R16.1; also elsewhere on the board
/Vref_opt: C39.1, U8.17 (VREF); also elsewhere on the board
GND: C13.2, C14.2, C15.2, C16.2, C17.2, C18.2, C19.2, C24.2, C26.2, C27.2, C28.2, C29.2, C30.2, C31.2, C43.2, R9.1, R12.2, R23.2, R24.2, U5.2 (GND), U6.1 (GND), U7.2 (PGND), U7.3 (PGND), U7.4 (PGND), U7.6 (PGND), U7.7 (MODE); also elsewhere on the board
unnamed: C20.2, R14.1, U7.11 (AGND)
unnamed: C21.2, R9.2, R10.2, U5.5 (FB)
unnamed: C22.1, U6.6 (VBST)
unnamed: C22.2, L2.1, U6.2 (SW)
unnamed: C23.2, R11.1, R12.1, U6.4 (FB)
unnamed: C25.1, L3.1, TP5.1, U7.8 (SW)
unnamed: C25.2, U7.9 (BST)
unnamed: C32.1, R17.1, TP_Cell3.1, U8.3 (VC6)
unnamed: C32.2, C33.1, R18.1, TP_Cell2.1, U8.4 (VC5), U8.5 (VC4), U8.6 (VC3), U8.7 (VC2)
unnamed: C33.2, C34.1, R19.1, TP_Cell1.1, U8.8 (VC1)
unnamed: C36.1, R20.1, TP_Cell0.1, U8.9 (VC0)
unnamed: C38.1, R21.1, U8.1 (VCTL), U8.2 (BAT)
unnamed: C41.1, U8.20 (V3P3)
unnamed: C42.1, R23.1, U8.12 (SENSEP)
unnamed: C42.2, R25.1, U8.11 (SENSEN)
unnamed: L1.1, TP3.1, U5.7 (SW)
unnamed: R13.1, R14.2, U7.12 (FB)
unnamed: R22.2, U8.16 (VTB)
unnamed: U5.4 (SGND), U5.8 (VOUT)

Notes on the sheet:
Battery Management System
High current ground plate
Raspberry Pi Buck
5V Buck Ultrasonic
3V3 Buck MCU
Battery Bulk Capacitance

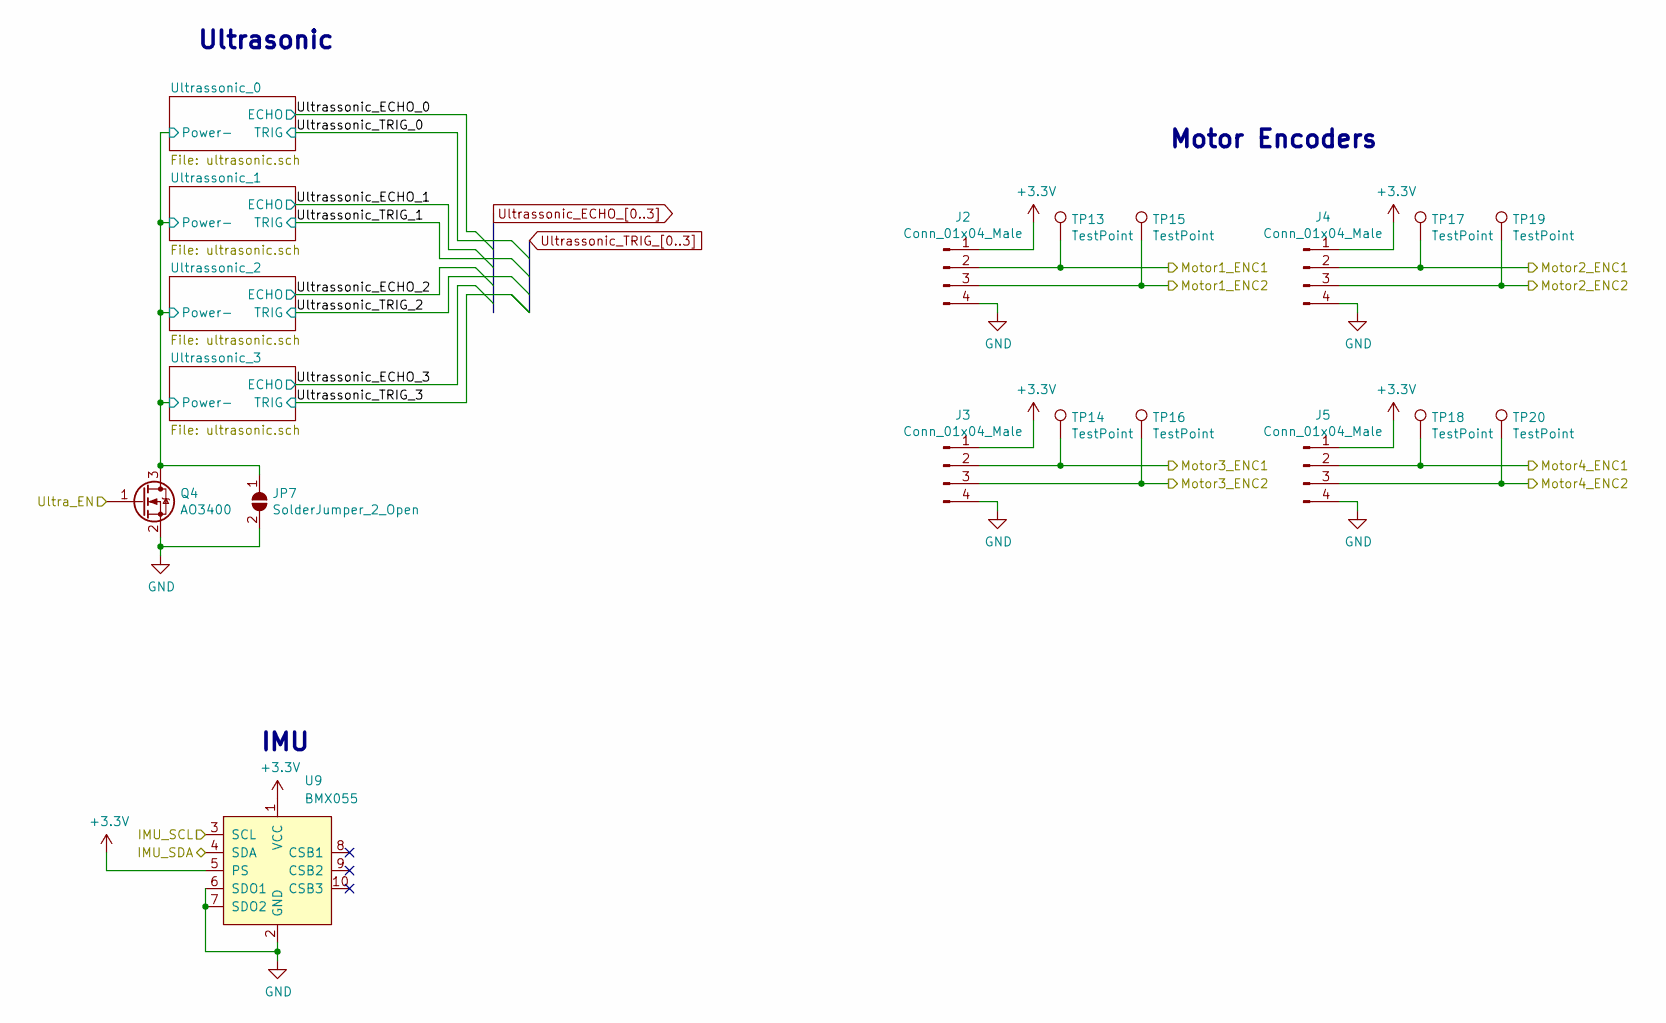
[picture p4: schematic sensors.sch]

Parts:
J2, J3, J4, J5: Conn_01x04_Male; JST_XH_S4B-XH-A-1_1x04_P2.50mm_Horizontal
JP7: SolderJumper_2_Open; SolderJumper-2_P1.3mm_Open_Pad1.0x1.5mm
Q4: AO3400; SOT-23
TP13, TP14, TP15, TP16, TP17, TP18, TP19, TP20: TestPoint; TestPoint_Pad_D1.0mm
U9: BMX055; PinSocket_1x10_P2.54mm_Vertical

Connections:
+3V3: J2.1, J3.1, J4.1, J5.1, U9.1 (VCC), U9.5 (PS); also elsewhere on the board
/I2C2_SCL: U9.3 (SCL); also elsewhere on the board
/I2C2_SDA: U9.4 (SDA); also elsewhere on the board
/Motor1_ENC1: J2.2, TP13.1; also elsewhere on the board
/Motor1_ENC2: J2.3, TP15.1; also elsewhere on the board
/Motor2_ENC1: J4.2, TP17.1; also elsewhere on the board
/Motor2_ENC2: J4.3, TP19.1; also elsewhere on the board
/Motor3_ENC1: J3.2, TP14.1; also elsewhere on the board
/Motor3_ENC2: J3.3, TP16.1; also elsewhere on the board
/Motor4_ENC1: J5.2, TP18.1; also elsewhere on the board
/Motor4_ENC2: J5.3, TP20.1; also elsewhere on the board
/Sensors/Ultrassonic_0/Power-: JP7.1 (A), Q4.3 (D); also elsewhere on the board
/Ultra_EN: Q4.1 (G); also elsewhere on the board
GND: J2.4, J3.4, J4.4, J5.4, JP7.2 (B), Q4.2 (S), U9.2 (GND), U9.6 (SDO1), U9.7 (SDO2); also elsewhere on the board

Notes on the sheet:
Motor Encoders
Ultrasonic
IMU

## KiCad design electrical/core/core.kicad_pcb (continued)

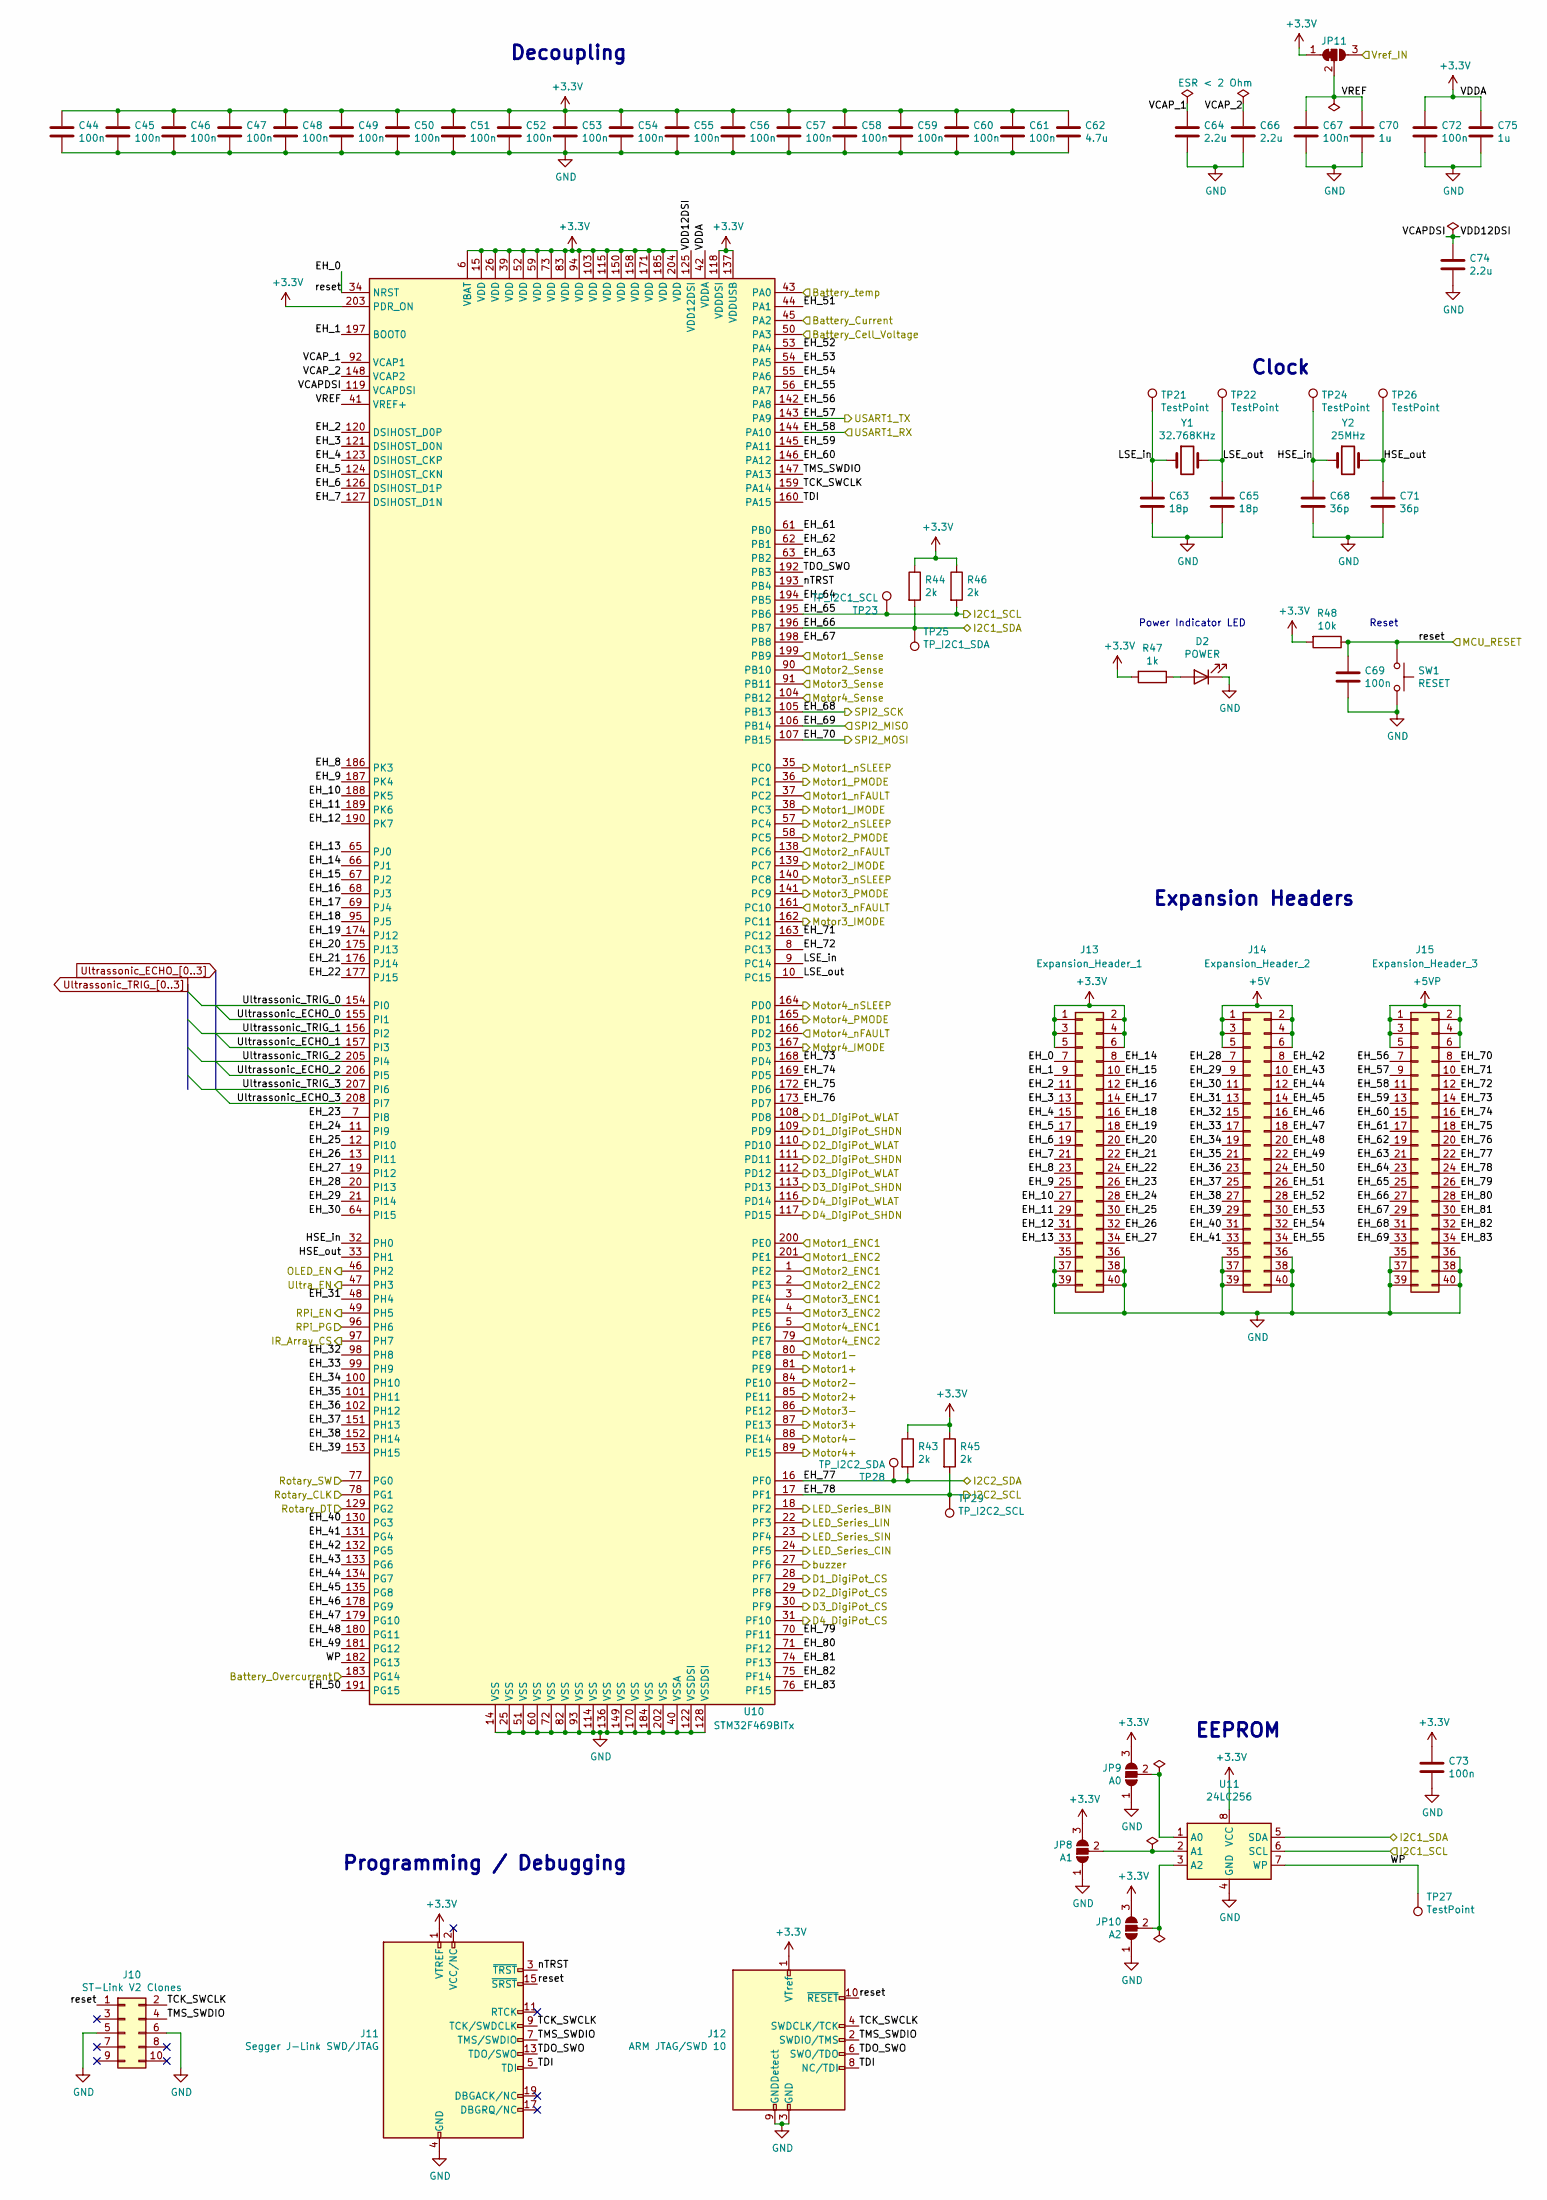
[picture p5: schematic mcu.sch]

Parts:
C44, C45, C46, C47, C48, C49, C50, C51, C52, C53, C54, C55, C56, C57, C58, C59, C60, C61, C67, C69, C72, C73: 100n; C_0603_1608Metric
C62: 4.7u; C_0603_1608Metric
C63, C65: 18p; C_0603_1608Metric
C64, C66, C74: 2.2u; C_0603_1608Metric
C68, C71: 36p; C_0603_1608Metric
C70, C75: 1u; C_0603_1608Metric
D2: POWER; LED_0805_2012Metric
J10: ST-Link V2 Clones; IDC-Header_2x05_P2.54mm_Vertical
J11: Segger J-Link SWD/JTAG; IDC-Header_2x10_P2.54mm_Vertical
J12: ARM JTAG/SWD 10; IDC-Header_2x05_P2.54mm_Vertical
J13: Expansion_Header_1; IDC-Header_2x20_P2.54mm_Vertical
J14: Expansion_Header_2; IDC-Header_2x20_P2.54mm_Vertical
J15: Expansion_Header_3; IDC-Header_2x20_P2.54mm_Vertical
JP8: A1; SolderJumper-3_P1.3mm_Open_Pad1.0x1.5mm
JP9: A0; SolderJumper-3_P1.3mm_Open_Pad1.0x1.5mm
JP10: A2; SolderJumper-3_P1.3mm_Open_Pad1.0x1.5mm
JP11: Vref_select; SolderJumper-3_P1.3mm_Bridged12_RoundedPad1.0x1.5mm_NumberL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
R43, R44, R45, R46: 2k; R_0603_1608Metric
R47: 1k; R_0603_1608Metric
R48: 10k; R_0603_1608Metric
SW1: RESET; SW_PUSH_6mm
TP21, TP22, TP24, TP26, TP27: TestPoint; TestPoint_Pad_D1.0mm
TP23: TP_I2C1_SCL; TestPoint_Pad_D1.0mm
TP25: TP_I2C1_SDA; TestPoint_Pad_D1.0mm
TP28: TP_I2C2_SDA; TestPoint_Pad_D1.0mm
TP29: TP_I2C2_SCL; TestPoint_Pad_D1.0mm
U10: STM32F469BITx; LQFP-208_28x28mm_P0.5mm
U11: 24LC256; SOIC-8_3.9x4.9mm_P1.27mm
Y1: 32.768KHz; Crystal_SMD_2520-4Pin_2.5x2.0mm
Y2: 25MHz; Crystal_SMD_2520-4Pin_2.5x2.0mm

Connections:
+3V3: C44.1, C45.1, C46.1, C47.1, C48.1, C49.1, C50.1, C51.1, C52.1, C53.1, C54.1, C55.1, C56.1, C57.1, C58.1, C59.1, C60.1, C61.1, C62.1, C72.1, C73.1, C75.1, J11.1 (VTREF), J12.1 (VTref), J13.1, J13.2, J13.3, J13.4, J13.5, J13.6, JP8.3 (B), JP9.3 (B), JP10.3 (B), JP11.1 (A), R43.1, R44.1, R45.1, R46.1, R47.2, R48.2, U10.6 (VBAT), U10.15 (VDD), U10.26 (VDD), U10.39 (VDD), U10.42 (VDDA), U10.52 (VDD), U10.59 (VDD), U10.73 (VDD), U10.83 (VDD), U10.94 (VDD), U10.103 (VDD), U10.115 (VDD), U10.118 (VDDDSI), U10.137 (VDDUSB), U10.150 (VDD), U10.158 (VDD), U10.171 (VDD), U10.185 (VDD), U10.203 (PDR_ON), U10.204 (VDD), U11.8 (VCC); also elsewhere on the board
+5V: J14.1, J14.2, J14.3, J14.4, J14.5, J14.6; also elsewhere on the board
+5VP: J15.1, J15.2, J15.3, J15.4, J15.5, J15.6; also elsewhere on the board
/Battery_Cell_Voltage: U10.50 (PA3); also elsewhere on the board
/Battery_Current: U10.45 (PA2); also elsewhere on the board
/Battery_Overcurrent: U10.183 (PG14); also elsewhere on the board
/Battery_Temperature: U10.43 (PA0); also elsewhere on the board
/D1_DigiPot_CS: U10.28 (PF7); also elsewhere on the board
/D1_DigiPot_SHDN: U10.109 (PD9); also elsewhere on the board
/D1_DigiPot_WLAT: U10.108 (PD8); also elsewhere on the board
/D1_IMODE: U10.38 (PC3); also elsewhere on the board
/D1_IN1: U10.80 (PE8); also elsewhere on the board
/D1_IN2: U10.81 (PE9); also elsewhere on the board
/D1_PMODE: U10.36 (PC1); also elsewhere on the board
/D1_SENSE: U10.199 (PB9); also elsewhere on the board
/D1_nFAULT: U10.37 (PC2); also elsewhere on the board
/D1_nSLEEP: U10.35 (PC0); also elsewhere on the board
/D2_DigiPot_CS: U10.29 (PF8); also elsewhere on the board
/D2_DigiPot_SHDN: U10.111 (PD11); also elsewhere on the board
/D2_DigiPot_WLAT: U10.110 (PD10); also elsewhere on the board
/D2_IMODE: U10.139 (PC7); also elsewhere on the board
/D2_IN1: U10.84 (PE10); also elsewhere on the board
/D2_IN2: U10.85 (PE11); also elsewhere on the board
/D2_PMODE: U10.58 (PC5); also elsewhere on the board
/D2_SENSE: U10.90 (PB10); also elsewhere on the board
/D2_nFAULT: U10.138 (PC6); also elsewhere on the board
/D2_nSLEEP: U10.57 (PC4); also elsewhere on the board
/D3_DigiPot_CS: U10.30 (PF9); also elsewhere on the board
/D3_DigiPot_SHDN: U10.113 (PD13); also elsewhere on the board
/D3_DigiPot_WLAT: U10.112 (PD12); also elsewhere on the board
/D3_IMODE: U10.162 (PC11); also elsewhere on the board
/D3_IN1: U10.86 (PE12); also elsewhere on the board
/D3_IN2: U10.87 (PE13); also elsewhere on the board
/D3_PMODE: U10.141 (PC9); also elsewhere on the board
/D3_SENSE: U10.91 (PB11); also elsewhere on the board
/D3_nFAULT: U10.161 (PC10); also elsewhere on the board
/D3_nSLEEP: U10.140 (PC8); also elsewhere on the board
/D4_DigiPot_CS: U10.31 (PF10); also elsewhere on the board
/D4_DigiPot_SHDN: U10.117 (PD15); also elsewhere on the board
/D4_DigiPot_WLAT: U10.116 (PD14); also elsewhere on the board
/D4_IMODE: U10.167 (PD3); also elsewhere on the board
/D4_IN1: U10.88 (PE14); also elsewhere on the board
/D4_IN2: U10.89 (PE15); also elsewhere on the board
/D4_PMODE: U10.165 (PD1); also elsewhere on the board
/D4_SENSE: U10.104 (PB12); also elsewhere on the board
/D4_nFAULT: U10.166 (PD2); also elsewhere on the board
/D4_nSLEEP: U10.164 (PD0); also elsewhere on the board
/I2C1_SCL: J15.25, R46.2, TP23.1, U10.195 (PB6), U11.6 (SCL); also elsewhere on the board
/I2C1_SDA: J15.27, R44.2, TP25.1, U10.196 (PB7), U11.5 (SDA); also elsewhere on the board
/I2C2_SCL: J15.24, R45.2, TP29.1, U10.17 (PF1); also elsewhere on the board
/I2C2_SDA: J15.22, R43.2, TP28.1, U10.16 (PF0); also elsewhere on the board
/IR_Array_CS: U10.97 (PH7); also elsewhere on the board
/LED_Series_BIN: U10.18 (PF2); also elsewhere on the board
/LED_Series_CIN: U10.24 (PF5); also elsewhere on the board
/LED_Series_LIN: U10.22 (PF3); also elsewhere on the board
/LED_Series_SIN: U10.23 (PF4); also elsewhere on the board
/MCU/EH_1: J13.9, U10.197 (BOOT0)
/MCU/EH_2: J13.11, U10.120 (DSIHOST_D0P)
/MCU/EH_3: J13.13, U10.121 (DSIHOST_D0N)
/MCU/EH_4: J13.15, U10.123 (DSIHOST_CKP)
/MCU/EH_5: J13.17, U10.124 (DSIHOST_CKN)
/MCU/EH_6: J13.19, U10.126 (DSIHOST_D1P)
/MCU/EH_7: J13.21, U10.127 (DSIHOST_D1N)
/MCU/EH_8: J13.23, U10.186 (PK3)
/MCU/EH_9: J13.25, U10.187 (PK4)
/MCU/EH_10: J13.27, U10.188 (PK5)
/MCU/EH_11: J13.29, U10.189 (PK6)
/MCU/EH_12: J13.31, U10.190 (PK7)
/MCU/EH_13: J13.33, U10.65 (PJ0)
/MCU/EH_14: J13.8, U10.66 (PJ1)
/MCU/EH_15: J13.10, U10.67 (PJ2)
/MCU/EH_16: J13.12, U10.68 (PJ3)
/MCU/EH_17: J13.14, U10.69 (PJ4)
/MCU/EH_18: J13.16, U10.95 (PJ5)
/MCU/EH_19: J13.18, U10.174 (PJ12)
/MCU/EH_20: J13.20, U10.175 (PJ13)
/MCU/EH_21: J13.22, U10.176 (PJ14)
/MCU/EH_22: J13.24, U10.177 (PJ15)
/MCU/EH_23: J13.26, U10.7 (PI8)
/MCU/EH_24: J13.28, U10.11 (PI9)
/MCU/EH_25: J13.30, U10.12 (PI10)
/MCU/EH_26: J13.32, U10.13 (PI11)
/MCU/EH_27: J13.34, U10.19 (PI12)
/MCU/EH_28: J14.7, U10.20 (PI13)
/MCU/EH_29: J14.9, U10.21 (PI14)
/MCU/EH_30: J14.11, U10.64 (PI15)
/MCU/EH_31: J14.13, U10.48 (PH4)
/MCU/EH_32: J14.15, U10.98 (PH8)
/MCU/EH_33: J14.17, U10.99 (PH9)
/MCU/EH_34: J14.19, U10.100 (PH10)
/MCU/EH_35: J14.21, U10.101 (PH11)
/MCU/EH_36: J14.23, U10.102 (PH12)
/MCU/EH_37: J14.25, U10.151 (PH13)
/MCU/EH_38: J14.27, U10.152 (PH14)
/MCU/EH_39: J14.29, U10.153 (PH15)
/MCU/EH_40: J14.31, U10.130 (PG3)
/MCU/EH_41: J14.33, U10.131 (PG4)
/MCU/EH_42: J14.8, U10.132 (PG5)
/MCU/EH_43: J14.10, U10.133 (PG6)
/MCU/EH_44: J14.12, U10.134 (PG7)
/MCU/EH_45: J14.14, U10.135 (PG8)
/MCU/EH_46: J14.16, U10.178 (PG9)
/MCU/EH_47: J14.18, U10.179 (PG10)
/MCU/EH_48: J14.20, U10.180 (PG11)
/MCU/EH_49: J14.22, U10.181 (PG12)
/MCU/EH_50: J14.24, U10.191 (PG15)
/MCU/EH_51: J14.26, U10.44 (PA1)
/MCU/EH_52: J14.28, U10.53 (PA4)
/MCU/EH_53: J14.30, U10.54 (PA5)
/MCU/EH_54: J14.32, U10.55 (PA6)
/MCU/EH_55: J14.34, U10.56 (PA7)
/MCU/EH_56: J15.7, U10.142 (PA8)
/MCU/EH_59: J15.13, U10.145 (PA11)
/MCU/EH_60: J15.15, U10.146 (PA12)
/MCU/EH_61: J15.17, U10.61 (PB0)
/MCU/EH_62: J15.19, U10.62 (PB1)
/MCU/EH_63: J15.21, U10.63 (PB2)
/MCU/EH_64: J15.23, U10.194 (PB5)
/MCU/EH_67: J15.29, U10.198 (PB8)
/MCU/EH_71: J15.10, U10.163 (PC12)
/MCU/EH_72: J15.12, U10.8 (PC13)
/MCU/EH_73: J15.14, U10.168 (PD4)
/MCU/EH_74: J15.16, U10.169 (PD5)
/MCU/EH_75: J15.18, U10.172 (PD6)
/MCU/EH_76: J15.20, U10.173 (PD7)
/MCU/EH_79: J15.26, U10.70 (PF11)
/MCU/EH_80: J15.28, U10.71 (PF12)
/MCU/EH_81: J15.30, U10.74 (PF13)
/MCU/EH_82: J15.32, U10.75 (PF14)
/MCU/EH_83: J15.34, U10.76 (PF15)
/MCU/HSE_in: C68.1, TP24.1, U10.32 (PH0), Y2.1
/MCU/HSE_out: C71.1, TP26.1, U10.33 (PH1), Y2.2
/MCU/LSE_in: C63.1, TP21.1, U10.9 (PC14), Y1.1
/MCU/LSE_out: C65.1, TP22.1, U10.10 (PC15), Y1.2
/MCU/TCK_SWCLK: J10.2, J11.9 (TCK/SWDCLK), J12.4 (SWDCLK/TCK), U10.159 (PA14)
/MCU/TDI: J11.5 (TDI), J12.8 (NC/TDI), U10.160 (PA15)
/MCU/TDO_SWO: J11.13 (TDO/SWO), J12.6 (SWO/TDO), U10.192 (PB3)
/MCU/TMS_SWDIO: J10.4, J11.7 (TMS/SWDIO), J12.2 (SWDIO/TMS), U10.147 (PA13)
/MCU/VCAPDSI: C74.1, U10.119 (VCAPDSI), U10.125 (VDD12DSI)
/MCU/VCAP_1: C64.1, U10.92 (VCAP1)
/MCU/VCAP_2: C66.1, U10.148 (VCAP2)
/MCU/VREF: C67.1, C70.1, JP11.2 (C), U10.41 (VREF+)
/MCU/WP: TP27.1, U10.182 (PG13), U11.7 (WP)
/MCU/nTRST: J11.3 (~TRST~), U10.193 (PB4)
/MCU_RESET: C69.1, J10.1, J11.15 (~SRST~), J12.10 (~RESET~), J13.7, R48.1, SW1.1, U10.34 (NRST); also elsewhere on the board
/Motor1_ENC1: U10.200 (PE0); also elsewhere on the board
/Motor1_ENC2: U10.201 (PE1); also elsewhere on the board
/Motor2_ENC1: U10.1 (PE2); also elsewhere on the board
/Motor2_ENC2: U10.2 (PE3); also elsewhere on the board
/Motor3_ENC1: U10.3 (PE4); also elsewhere on the board
/Motor3_ENC2: U10.4 (PE5); also elsewhere on the board
/Motor4_ENC1: U10.5 (PE6); also elsewhere on the board
/Motor4_ENC2: U10.79 (PE7); also elsewhere on the board
/OLED_EN: U10.46 (PH2); also elsewhere on the board
/RPi_EN: U10.49 (PH5); also elsewhere on the board
/RPi_PG: U10.96 (PH6); also elsewhere on the board
/RPi_RX: J15.9, U10.143 (PA9); also elsewhere on the board
/RPi_TX: J15.11, U10.144 (PA10); also elsewhere on the board
/Rotary_CLK: U10.78 (PG1); also elsewhere on the board
/Rotary_DT: U10.129 (PG2); also elsewhere on the board
/Rotary_SW: U10.77 (PG0); also elsewhere on the board
/SPI2_MISO: J15.33, U10.106 (PB14); also elsewhere on the board
/SPI2_MOSI: J15.8, U10.107 (PB15); also elsewhere on the board
/SPI2_SCK: J15.31, U10.105 (PB13); also elsewhere on the board
/Ultra_EN: U10.47 (PH3); also elsewhere on the board
/Vref_opt: JP11.3 (B); also elsewhere on the board
/buzzer: U10.27 (PF6); also elsewhere on the board
GND: C44.2, C45.2, C46.2, C47.2, C48.2, C49.2, C50.2, C51.2, C52.2, C53.2, C54.2, C55.2, C56.2, C57.2, C58.2, C59.2, C60.2, C61.2, C62.2, C63.2, C64.2, C65.2, C66.2, C67.2, C68.2, C69.2, C70.2, C71.2, C72.2, C73.2, C74.2, C75.2, D2.1 (K), J10.5, J10.6, J11.4 (GND), J11.6 (GND), J11.8 (GND), J11.10 (GND), J11.12 (GND), J11.14 (GND), J11.16 (GND), J11.18 (GND), J11.20 (GND), J12.3 (GND), J12.5 (GND), J12.9 (GNDDetect), J13.35, J13.36, J13.37, J13.38, J13.39, J13.40, J14.35, J14.36, J14.37, J14.38, J14.39, J14.40, J15.35, J15.36, J15.37, J15.38, J15.39, J15.40, JP8.1 (A), JP9.1 (A), JP10.1 (A), SW1.2, U10.14 (VSS), U10.25 (VSS), U10.40 (VSSA), U10.51 (VSS), U10.60 (VSS), U10.72 (VSS), U10.82 (VSS), U10.93 (VSS), U10.114 (VSS), U10.122 (VSSDSI), U10.128 (VSSDSI), U10.136 (VSS), U10.149 (VSS), U10.170 (VSS), U10.184 (VSS), U10.202 (VSS), U11.4 (GND); also elsewhere on the board
unnamed: D2.2 (A), R47.1
unnamed: JP8.2 (C), U11.2 (A1)
unnamed: JP9.2 (C), U11.1 (A0)
unnamed: JP10.2 (C), U11.3 (A2)
Ultrassonic_ECHO_0: U10.155 (PI1); also elsewhere on the board
Ultrassonic_ECHO_1: U10.157 (PI3); also elsewhere on the board
Ultrassonic_ECHO_2: U10.206 (PI5); also elsewhere on the board
Ultrassonic_ECHO_3: U10.208 (PI7); also elsewhere on the board
Ultrassonic_TRIG_0: U10.154 (PI0); also elsewhere on the board
Ultrassonic_TRIG_1: U10.156 (PI2); also elsewhere on the board
Ultrassonic_TRIG_2: U10.205 (PI4); also elsewhere on the board
Ultrassonic_TRIG_3: U10.207 (PI6); also elsewhere on the board

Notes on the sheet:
Decoupling
Clock
Programming / Debugging
EEPROM
Reset
Power Indicator LED
Expansion Headers

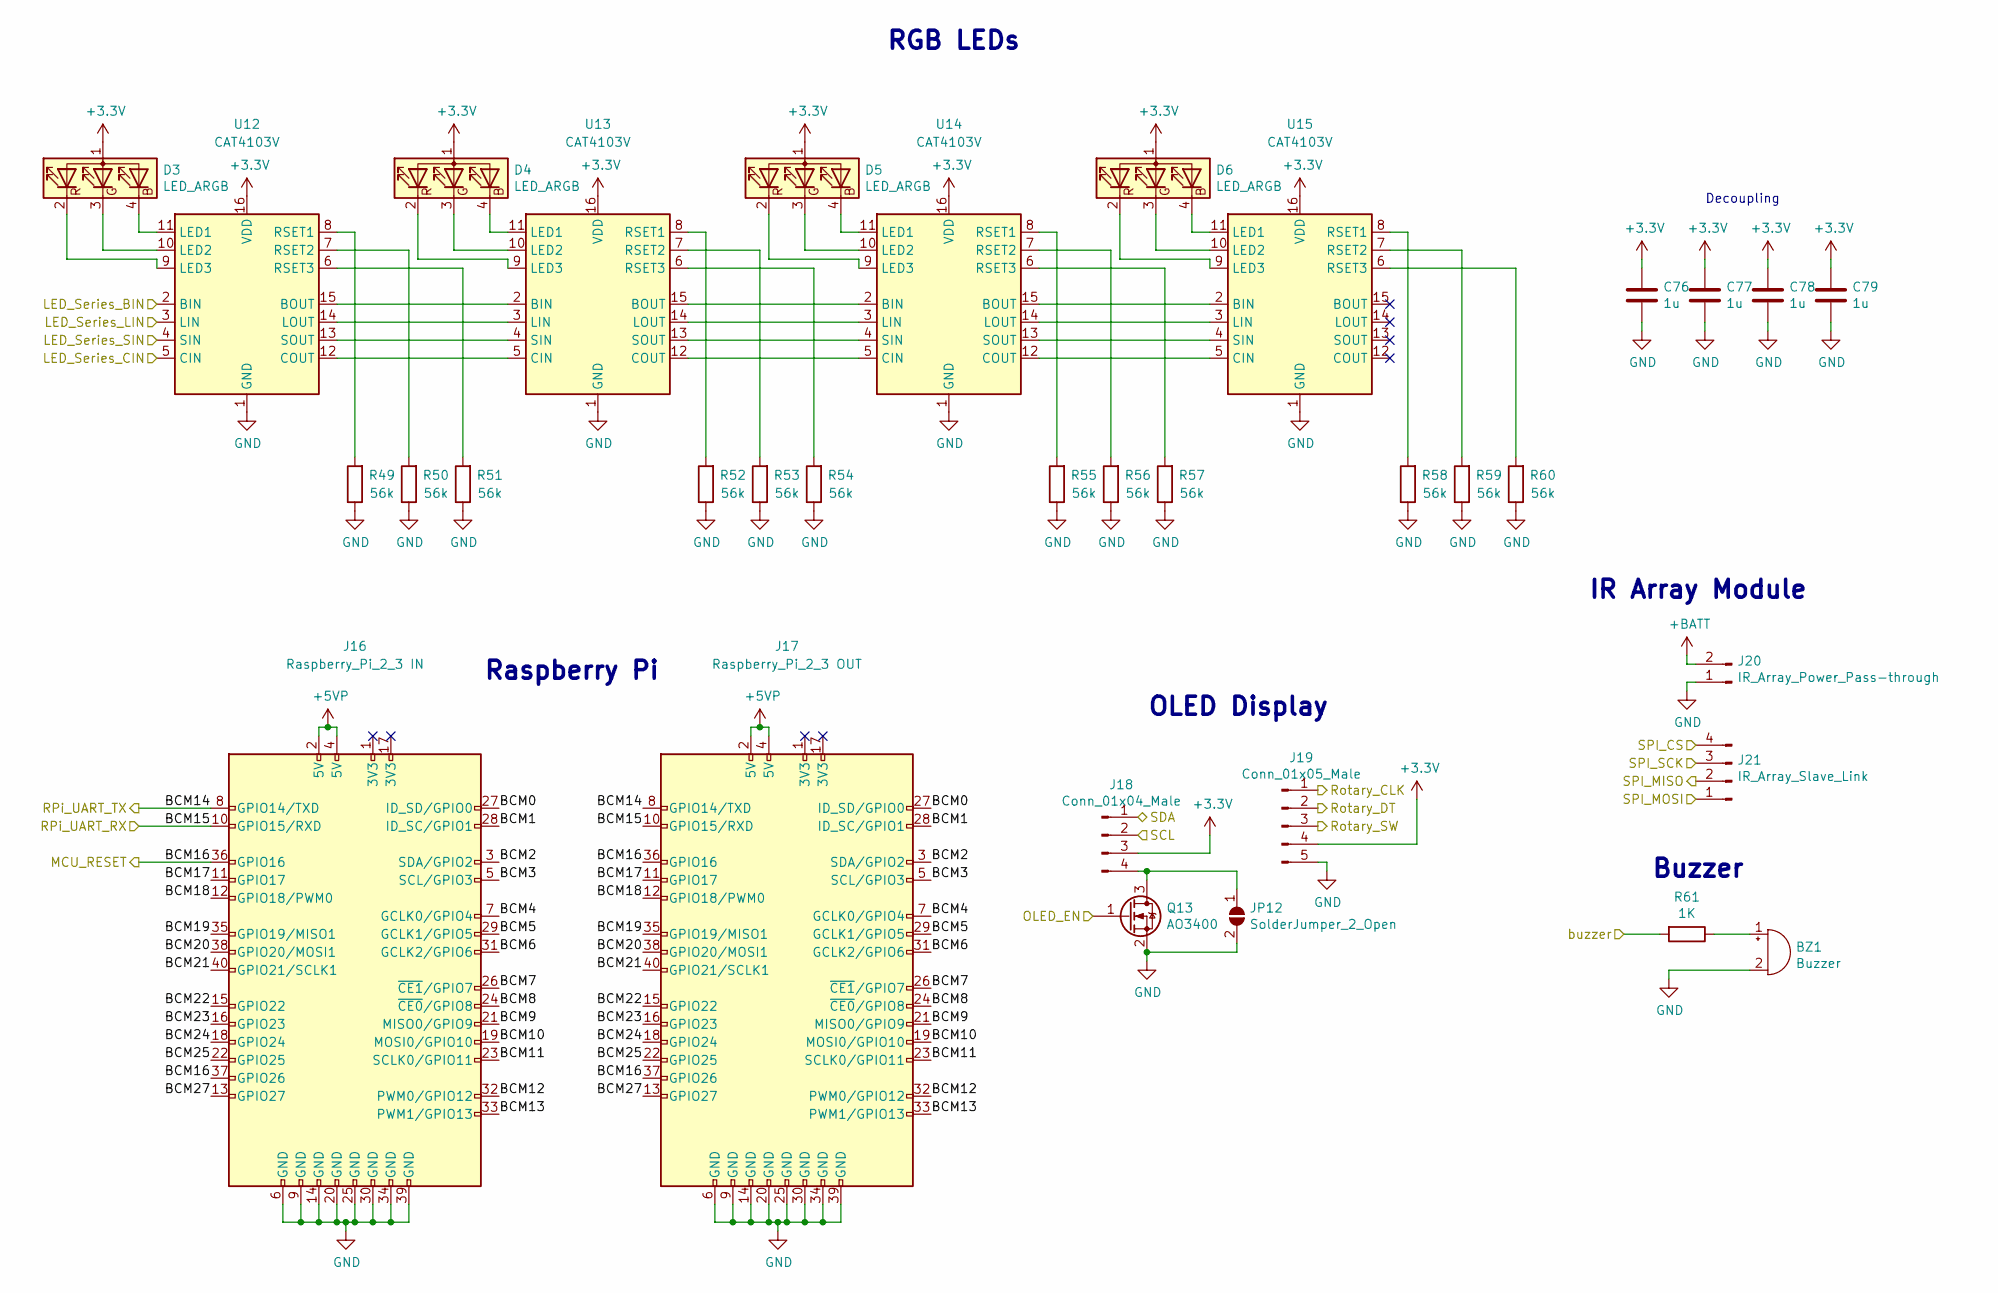
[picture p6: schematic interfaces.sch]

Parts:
BZ1: Buzzer; Buzzer_12x9.5RM7.6
C76, C77, C78, C79: 1u; C_0603_1608Metric
D3, D4, D5, D6: LED_ARGB; JST_XH_B4B-XH-A_1x04_P2.50mm_Vertical
J16: Raspberry_Pi_2_3 IN; IDC-Header_2x20_P2.54mm_Vertical
J17: Raspberry_Pi_2_3 OUT; IDC-Header_2x20_P2.54mm_Vertical
J18: Conn_01x04_Male; PinHeader_1x04_P2.54mm_Vertical
J19: Conn_01x05_Male; PinHeader_1x05_P2.54mm_Vertical
J20: IR_Array_Power_Pass-through; JST_XH_S2B-XH-A-1_1x02_P2.50mm_Horizontal
J21: IR_Array_Slave_Link; PinHeader_1x04_P2.54mm_Vertical
JP12: SolderJumper_2_Open; SolderJumper-2_P1.3mm_Open_Pad1.0x1.5mm
Q13: AO3400; SOT-23
R49, R50, R51, R52, R53, R54, R55, R56, R57, R58, R59, R60: 56k; R_0603_1608Metric
R61: 1K; R_0603_1608Metric
U12, U13, U14, U15: CAT4103V; SOIC-16_3.9x9.9mm_P1.27mm

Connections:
+3V3: C76.1, C77.1, C78.1, C79.1, D3.1 (A), D4.1 (A), D5.1 (A), D6.1 (A), J18.3, J19.4, U12.16 (VDD), U13.16 (VDD), U14.16 (VDD), U15.16 (VDD); also elsewhere on the board
+5VP: J16.2 (5V), J16.4 (5V), J17.2 (5V), J17.4 (5V); also elsewhere on the board
+BATT: J20.2; also elsewhere on the board
/I2C1_SCL: J18.2; also elsewhere on the board
/I2C1_SDA: J18.1; also elsewhere on the board
/IR_Array_CS: J21.4; also elsewhere on the board
/Interfaces/BCM0: J16.27 (ID_SD/GPIO0), J17.27 (ID_SD/GPIO0)
/Interfaces/BCM1: J16.28 (ID_SC/GPIO1), J17.28 (ID_SC/GPIO1)
/Interfaces/BCM2: J16.3 (SDA/GPIO2), J17.3 (SDA/GPIO2)
/Interfaces/BCM3: J16.5 (SCL/GPIO3), J17.5 (SCL/GPIO3)
/Interfaces/BCM4: J16.7 (GCLK0/GPIO4), J17.7 (GCLK0/GPIO4)
/Interfaces/BCM5: J16.29 (GCLK1/GPIO5), J17.29 (GCLK1/GPIO5)
/Interfaces/BCM6: J16.31 (GCLK2/GPIO6), J17.31 (GCLK2/GPIO6)
/Interfaces/BCM7: J16.26 (~CE1~/GPIO7), J17.26 (~CE1~/GPIO7)
/Interfaces/BCM8: J16.24 (~CE0~/GPIO8), J17.24 (~CE0~/GPIO8)
/Interfaces/BCM9: J16.21 (MISO0/GPIO9), J17.21 (MISO0/GPIO9)
/Interfaces/BCM10: J16.19 (MOSI0/GPIO10), J17.19 (MOSI0/GPIO10)
/Interfaces/BCM11: J16.23 (SCLK0/GPIO11), J17.23 (SCLK0/GPIO11)
/Interfaces/BCM12: J16.32 (PWM0/GPIO12), J17.32 (PWM0/GPIO12)
/Interfaces/BCM13: J16.33 (PWM1/GPIO13), J17.33 (PWM1/GPIO13)
/Interfaces/BCM17: J16.11 (GPIO17), J17.11 (GPIO17)
/Interfaces/BCM18: J16.12 (GPIO18/PWM0), J17.12 (GPIO18/PWM0)
/Interfaces/BCM19: J16.35 (GPIO19/MISO1), J17.35 (GPIO19/MISO1)
/Interfaces/BCM20: J16.38 (GPIO20/MOSI1), J17.38 (GPIO20/MOSI1)
/Interfaces/BCM21: J16.40 (GPIO21/SCLK1), J17.40 (GPIO21/SCLK1)
/Interfaces/BCM22: J16.15 (GPIO22), J17.15 (GPIO22)
/Interfaces/BCM23: J16.16 (GPIO23), J17.16 (GPIO23)
/Interfaces/BCM24: J16.18 (GPIO24), J17.18 (GPIO24)
/Interfaces/BCM25: J16.22 (GPIO25), J17.22 (GPIO25)
/Interfaces/BCM27: J16.13 (GPIO27), J17.13 (GPIO27)
/LED_Series_BIN: U12.2 (BIN); also elsewhere on the board
/LED_Series_CIN: U12.5 (CIN); also elsewhere on the board
/LED_Series_LIN: U12.3 (LIN); also elsewhere on the board
/LED_Series_SIN: U12.4 (SIN); also elsewhere on the board
/MCU_RESET: J16.36 (GPIO16), J16.37 (GPIO26), J17.36 (GPIO16), J17.37 (GPIO26); also elsewhere on the board
/OLED_EN: Q13.1 (G); also elsewhere on the board
/RPi_RX: J16.10 (GPIO15/RXD), J17.10 (GPIO15/RXD); also elsewhere on the board
/RPi_TX: J16.8 (GPIO14/TXD), J17.8 (GPIO14/TXD); also elsewhere on the board
/Rotary_CLK: J19.1; also elsewhere on the board
/Rotary_DT: J19.2; also elsewhere on the board
/Rotary_SW: J19.3; also elsewhere on the board
/SPI2_MISO: J21.2; also elsewhere on the board
/SPI2_MOSI: J21.1; also elsewhere on the board
/SPI2_SCK: J21.3; also elsewhere on the board
/buzzer: R61.2; also elsewhere on the board
GND: BZ1.2 (+), C76.2, C77.2, C78.2, C79.2, J16.6 (GND), J16.9 (GND), J16.14 (GND), J16.20 (GND), J16.25 (GND), J16.30 (GND), J16.34 (GND), J16.39 (GND), J17.6 (GND), J17.9 (GND), J17.14 (GND), J17.20 (GND), J17.25 (GND), J17.30 (GND), J17.34 (GND), J17.39 (GND), J19.5, J20.1, JP12.2 (B), Q13.2 (S), R49.1, R50.1, R51.1, R52.1, R53.1, R54.1, R55.1, R56.1, R57.1, R58.1, R59.1, R60.1, U12.1 (GND), U13.1 (GND), U14.1 (GND), U15.1 (GND); also elsewhere on the board
unnamed: BZ1.1 (-), R61.1
unnamed: D3.2 (RK), U12.9 (LED3)
unnamed: D3.3 (GK), U12.10 (LED2)
unnamed: D3.4 (BK), U12.11 (LED1)
unnamed: D4.2 (RK), U13.9 (LED3)
unnamed: D4.3 (GK), U13.10 (LED2)
unnamed: D4.4 (BK), U13.11 (LED1)
unnamed: D5.2 (RK), U14.9 (LED3)
unnamed: D5.3 (GK), U14.10 (LED2)
unnamed: D5.4 (BK), U14.11 (LED1)
unnamed: D6.2 (RK), U15.9 (LED3)
unnamed: D6.3 (GK), U15.10 (LED2)
unnamed: D6.4 (BK), U15.11 (LED1)
unnamed: J18.4, JP12.1 (A), Q13.3 (D)
unnamed: R49.2, U12.8 (RSET1)
unnamed: R50.2, U12.7 (RSET2)
unnamed: R51.2, U12.6 (RSET3)
unnamed: R52.2, U13.8 (RSET1)
unnamed: R53.2, U13.7 (RSET2)
unnamed: R54.2, U13.6 (RSET3)
unnamed: R55.2, U14.8 (RSET1)
unnamed: R56.2, U14.7 (RSET2)
unnamed: R57.2, U14.6 (RSET3)
unnamed: R58.2, U15.8 (RSET1)
unnamed: R59.2, U15.7 (RSET2)
unnamed: R60.2, U15.6 (RSET3)
unnamed: U12.12 (COUT), U13.5 (CIN)
unnamed: U12.13 (SOUT), U13.4 (SIN)
unnamed: U12.14 (LOUT), U13.3 (LIN)
unnamed: U12.15 (BOUT), U13.2 (BIN)
unnamed: U13.12 (COUT), U14.5 (CIN)
unnamed: U13.13 (SOUT), U14.4 (SIN)
unnamed: U13.14 (LOUT), U14.3 (LIN)
unnamed: U13.15 (BOUT), U14.2 (BIN)
unnamed: U14.12 (COUT), U15.5 (CIN)
unnamed: U14.13 (SOUT), U15.4 (SIN)
unnamed: U14.14 (LOUT), U15.3 (LIN)
unnamed: U14.15 (BOUT), U15.2 (BIN)

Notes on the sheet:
Buzzer
RGB LEDs
OLED Display
Raspberry Pi
Decoupling
IR Array Module

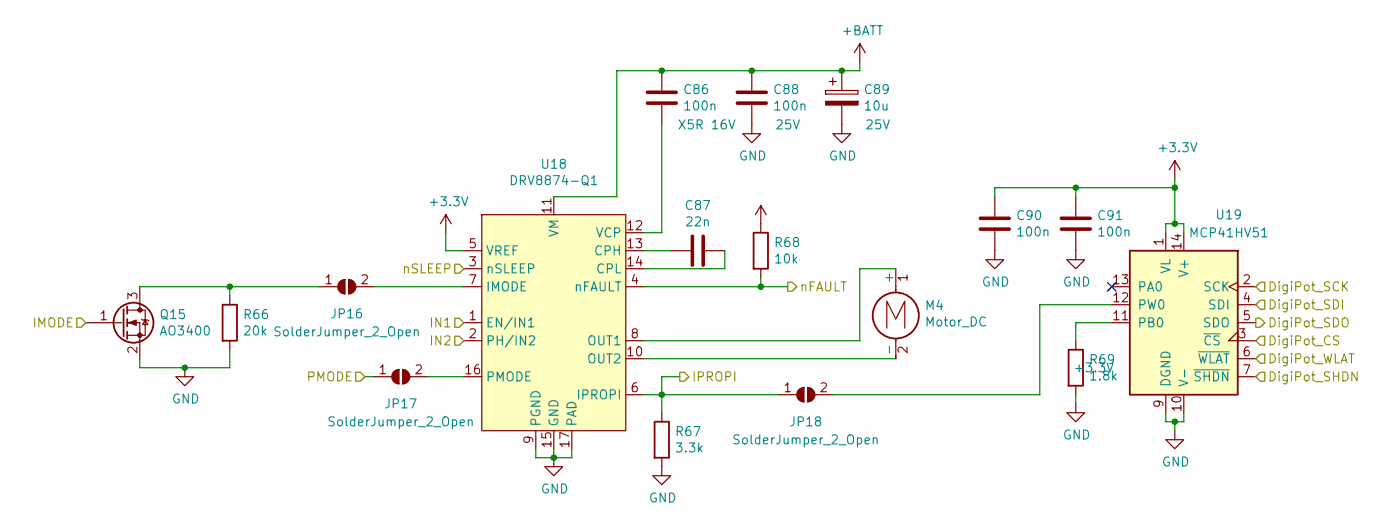
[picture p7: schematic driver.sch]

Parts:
C1, C3: 100n; C_1206_3216Metric
C2: 22n; C_1206_3216Metric
C4: 10u; CP_Elec_5x5.4
C5, C6: 100n; C_0603_1608Metric
JP1, JP2, JP3: SolderJumper_2_Open; SolderJumper-2_P1.3mm_Open_Pad1.0x1.5mm
M1: Motor_DC; TerminalBlock_bornier-2_P5.08mm
Q1: AO3400; SOT-23
R1: 20k; R_0603_1608Metric
R2: 3.3k; R_0603_1608Metric
R3: 10k; R_0603_1608Metric
R4: 1.8k; R_0603_1608Metric
U1: DRV8874-Q1; HTSSOP-16-1EP_4.4x5mm_P0.65mm_EP3.4x5mm_Mask2.46x2.31mm_The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
U2: MCP41HV51; TSSOP-14_4.4x5mm_P0.65mm

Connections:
+3V3: C5.1, C6.1, R3.1, U1.5 (VREF), U2.1 (VL), U2.14 (V+); also elsewhere on the board
+BATT: C1.1, C3.1, C4.1, U1.11 (VM); also elsewhere on the board
/D1_DigiPot_CS: U2.3 (~CS); also elsewhere on the board
/D1_DigiPot_SHDN: U2.7 (~SHDN); also elsewhere on the board
/D1_DigiPot_WLAT: U2.6 (~WLAT); also elsewhere on the board
/D1_IMODE: Q1.1 (G); also elsewhere on the board
/D1_IN1: U1.1 (EN/IN1); also elsewhere on the board
/D1_IN2: U1.2 (PH/IN2); also elsewhere on the board
/D1_PMODE: JP2.1 (A); also elsewhere on the board
/D1_SENSE: JP3.1 (A), R2.1, U1.6 (IPROPI); also elsewhere on the board
/D1_nFAULT: R3.2, U1.4 (nFAULT); also elsewhere on the board
/D1_nSLEEP: U1.3 (nSLEEP); also elsewhere on the board
/SPI2_MISO: U2.5 (SDO); also elsewhere on the board
/SPI2_MOSI: U2.4 (SDI); also elsewhere on the board
/SPI2_SCK: U2.2 (SCK); also elsewhere on the board
GND: C3.2, C4.2, C5.2, C6.2, Q1.2 (S), R1.2, R2.2, R4.2, U1.9 (PGND), U1.15 (GND), U1.17 (PAD), U2.9 (DGND), U2.10 (V-); also elsewhere on the board
unnamed: C1.2, U1.12 (VCP)
unnamed: C2.1, U1.14 (CPL)
unnamed: C2.2, U1.13 (CPH)
unnamed: JP1.1 (A), Q1.3 (D), R1.1
unnamed: JP1.2 (B), U1.7 (IMODE)
unnamed: JP2.2 (B), U1.16 (PMODE)
unnamed: JP3.2 (B), U2.12 (PW0)
unnamed: M1.1 (+), U1.8 (OUT1)
unnamed: M1.2 (-), U1.10 (OUT2)
unnamed: R4.1, U2.11 (PB0)

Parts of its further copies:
C7, C9, C80, C82, C86, C88: 100n; C_1206_3216Metric
C8, C81, C87: 22n; C_1206_3216Metric
C10, C83, C89: 10u; CP_Elec_5x5.4
C11, C12, C84, C85, C90, C91: 100n; C_0603_1608Metric
JP4, JP5, JP6, JP13, JP14, JP15, JP16, JP17, JP18: SolderJumper_2_Open; SolderJumper-2_P1.3mm_Open_Pad1.0x1.5mm
M2, M3, M4: Motor_DC; TerminalBlock_bornier-2_P5.08mm
Q2, Q14, Q15: AO3400; SOT-23
R5, R62, R66: 20k; R_0603_1608Metric
R6, R63, R67: 3.3k; R_0603_1608Metric
R7, R64, R68: 10k; R_0603_1608Metric
R8, R65, R69: 1.8k; R_0603_1608Metric
U3, U16, U18: DRV8874-Q1; HTSSOP-16-1EP_4.4x5mm_P0.65mm_EP3.4x5mm_Mask2.46x2.31mm_The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
U4, U17, U19: MCP41HV51; TSSOP-14_4.4x5mm_P0.65mm

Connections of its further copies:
+3V3: C11.1, C12.1, C84.1, C85.1, C90.1, C91.1, R7.1, R64.1, R68.1, U3.5 (VREF), U4.1 (VL), U4.14 (V+), U16.5 (VREF), U17.1 (VL), U17.14 (V+), U18.5 (VREF), U19.1 (VL), U19.14 (V+); also elsewhere on the board
+BATT: C7.1, C9.1, C10.1, C80.1, C82.1, C83.1, C86.1, C88.1, C89.1, U3.11 (VM), U16.11 (VM), U18.11 (VM); also elsewhere on the board
/D2_DigiPot_CS: U4.3 (~CS); also elsewhere on the board
/D2_DigiPot_SHDN: U4.7 (~SHDN); also elsewhere on the board
/D2_DigiPot_WLAT: U4.6 (~WLAT); also elsewhere on the board
/D2_IMODE: Q2.1 (G); also elsewhere on the board
/D2_IN1: U3.1 (EN/IN1); also elsewhere on the board
/D2_IN2: U3.2 (PH/IN2); also elsewhere on the board
/D2_PMODE: JP5.1 (A); also elsewhere on the board
/D2_SENSE: JP6.1 (A), R6.1, U3.6 (IPROPI); also elsewhere on the board
/D2_nFAULT: R7.2, U3.4 (nFAULT); also elsewhere on the board
/D2_nSLEEP: U3.3 (nSLEEP); also elsewhere on the board
/D3_DigiPot_CS: U17.3 (~CS); also elsewhere on the board
/D3_DigiPot_SHDN: U17.7 (~SHDN); also elsewhere on the board
/D3_DigiPot_WLAT: U17.6 (~WLAT); also elsewhere on the board
/D3_IMODE: Q14.1 (G); also elsewhere on the board
/D3_IN1: U16.1 (EN/IN1); also elsewhere on the board
/D3_IN2: U16.2 (PH/IN2); also elsewhere on the board
/D3_PMODE: JP14.1 (A); also elsewhere on the board
/D3_SENSE: JP15.1 (A), R63.1, U16.6 (IPROPI); also elsewhere on the board
/D3_nFAULT: R64.2, U16.4 (nFAULT); also elsewhere on the board
/D3_nSLEEP: U16.3 (nSLEEP); also elsewhere on the board
/D4_DigiPot_CS: U19.3 (~CS); also elsewhere on the board
/D4_DigiPot_SHDN: U19.7 (~SHDN); also elsewhere on the board
/D4_DigiPot_WLAT: U19.6 (~WLAT); also elsewhere on the board
/D4_IMODE: Q15.1 (G); also elsewhere on the board
/D4_IN1: U18.1 (EN/IN1); also elsewhere on the board
/D4_IN2: U18.2 (PH/IN2); also elsewhere on the board
/D4_PMODE: JP17.1 (A); also elsewhere on the board
/D4_SENSE: JP18.1 (A), R67.1, U18.6 (IPROPI); also elsewhere on the board
/D4_nFAULT: R68.2, U18.4 (nFAULT); also elsewhere on the board
/D4_nSLEEP: U18.3 (nSLEEP); also elsewhere on the board
/SPI2_MISO: U4.5 (SDO), U17.5 (SDO), U19.5 (SDO); also elsewhere on the board
/SPI2_MOSI: U4.4 (SDI), U17.4 (SDI), U19.4 (SDI); also elsewhere on the board
/SPI2_SCK: U4.2 (SCK), U17.2 (SCK), U19.2 (SCK); also elsewhere on the board
GND: C9.2, C10.2, C11.2, C12.2, C82.2, C83.2, C84.2, C85.2, C88.2, C89.2, C90.2, C91.2, Q2.2 (S), Q14.2 (S), Q15.2 (S), R5.2, R6.2, R8.2, R62.2, R63.2, R65.2, R66.2, R67.2, R69.2, U3.9 (PGND), U3.15 (GND), U3.17 (PAD), U4.9 (DGND), U4.10 (V-), U16.9 (PGND), U16.15 (GND), U16.17 (PAD), U17.9 (DGND), U17.10 (V-), U18.9 (PGND), U18.15 (GND), U18.17 (PAD), U19.9 (DGND), U19.10 (V-); also elsewhere on the board
unnamed: C7.2, U3.12 (VCP)
unnamed: C8.1, U3.14 (CPL)
unnamed: C8.2, U3.13 (CPH)
unnamed: C80.2, U16.12 (VCP)
unnamed: C81.1, U16.14 (CPL)
unnamed: C81.2, U16.13 (CPH)
unnamed: C86.2, U18.12 (VCP)
unnamed: C87.1, U18.14 (CPL)
unnamed: C87.2, U18.13 (CPH)
unnamed: JP4.1 (A), Q2.3 (D), R5.1
unnamed: JP4.2 (B), U3.7 (IMODE)
unnamed: JP5.2 (B), U3.16 (PMODE)
unnamed: JP6.2 (B), U4.12 (PW0)
unnamed: JP13.1 (A), Q14.3 (D), R62.1
unnamed: JP13.2 (B), U16.7 (IMODE)
unnamed: JP14.2 (B), U16.16 (PMODE)
unnamed: JP15.2 (B), U17.12 (PW0)
unnamed: JP16.1 (A), Q15.3 (D), R66.1
unnamed: JP16.2 (B), U18.7 (IMODE)
unnamed: JP17.2 (B), U18.16 (PMODE)
unnamed: JP18.2 (B), U19.12 (PW0)
unnamed: M2.1 (+), U3.8 (OUT1)
unnamed: M2.2 (-), U3.10 (OUT2)
unnamed: M3.1 (+), U16.8 (OUT1)
unnamed: M3.2 (-), U16.10 (OUT2)
unnamed: M4.1 (+), U18.8 (OUT1)
unnamed: M4.2 (-), U18.10 (OUT2)
unnamed: R8.1, U4.11 (PB0)
unnamed: R65.1, U17.11 (PB0)
unnamed: R69.1, U19.11 (PB0)

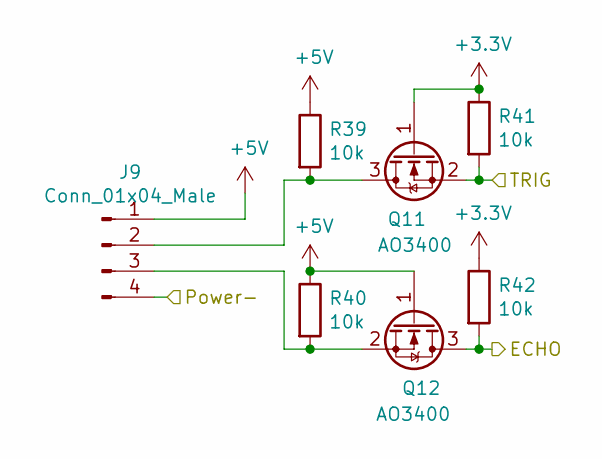
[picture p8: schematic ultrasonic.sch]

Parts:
J6: Conn_01x04_Male; PinHeader_1x04_P2.54mm_Vertical
Q5, Q6: AO3400; SOT-23
R27, R28, R29, R30: 10k; R_0603_1608Metric

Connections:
+3V3: Q5.1 (G), R29.1, R30.1; also elsewhere on the board
+5V: J6.1, Q6.1 (G), R27.1, R28.1; also elsewhere on the board
/Sensors/Ultrassonic_0/Power-: J6.4; also elsewhere on the board
unnamed: J6.2, Q5.3 (D), R27.2
unnamed: J6.3, Q6.2 (S), R28.2
Ultrassonic_ECHO_0: Q6.3 (D), R30.2; also elsewhere on the board
Ultrassonic_TRIG_0: Q5.2 (S), R29.2; also elsewhere on the board

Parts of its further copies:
J7, J8, J9: Conn_01x04_Male; PinHeader_1x04_P2.54mm_Vertical
Q7, Q8, Q9, Q10, Q11, Q12: AO3400; SOT-23
R31, R32, R33, R34, R35, R36, R37, R38, R39, R40, R41, R42: 10k; R_0603_1608Metric

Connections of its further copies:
+3V3: Q7.1 (G), Q9.1 (G), Q11.1 (G), R33.1, R34.1, R37.1, R38.1, R41.1, R42.1; also elsewhere on the board
+5V: J7.1, J8.1, J9.1, Q8.1 (G), Q10.1 (G), Q12.1 (G), R31.1, R32.1, R35.1, R36.1, R39.1, R40.1; also elsewhere on the board
/Sensors/Ultrassonic_0/Power-: J7.4, J8.4, J9.4; also elsewhere on the board
unnamed: J7.2, Q7.3 (D), R31.2
unnamed: J7.3, Q8.2 (S), R32.2
unnamed: J8.2, Q9.3 (D), R35.2
unnamed: J8.3, Q10.2 (S), R36.2
unnamed: J9.2, Q11.3 (D), R39.2
unnamed: J9.3, Q12.2 (S), R40.2
Ultrassonic_ECHO_1: Q8.3 (D), R34.2; also elsewhere on the board
Ultrassonic_ECHO_2: Q10.3 (D), R38.2; also elsewhere on the board
Ultrassonic_ECHO_3: Q12.3 (D), R42.2; also elsewhere on the board
Ultrassonic_TRIG_1: Q7.2 (S), R33.2; also elsewhere on the board
Ultrassonic_TRIG_2: Q9.2 (S), R37.2; also elsewhere on the board
Ultrassonic_TRIG_3: Q11.2 (S), R41.2; also elsewhere on the board

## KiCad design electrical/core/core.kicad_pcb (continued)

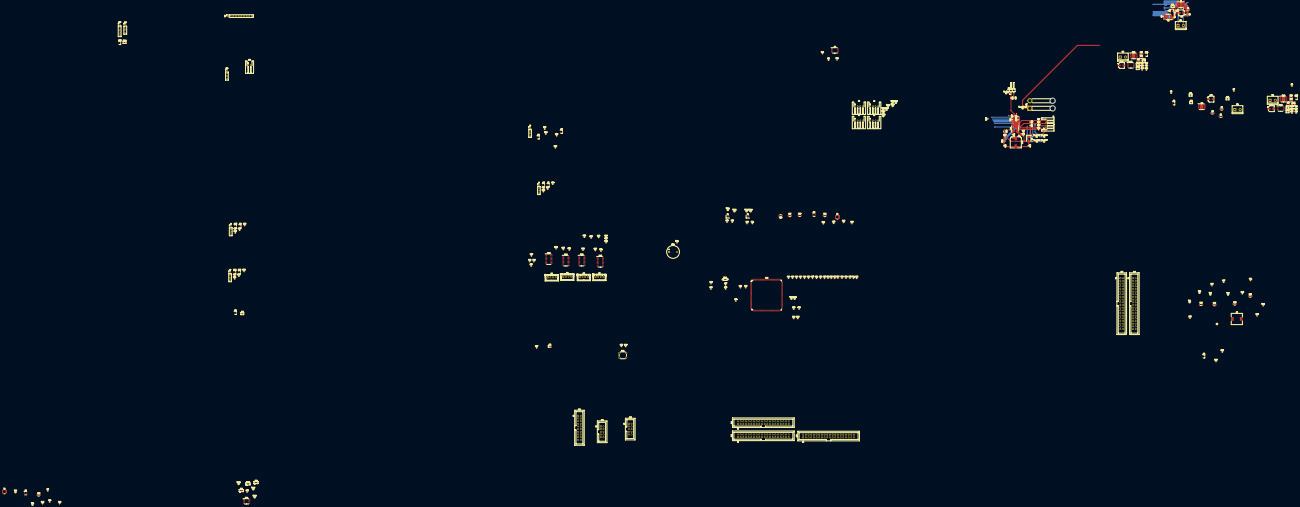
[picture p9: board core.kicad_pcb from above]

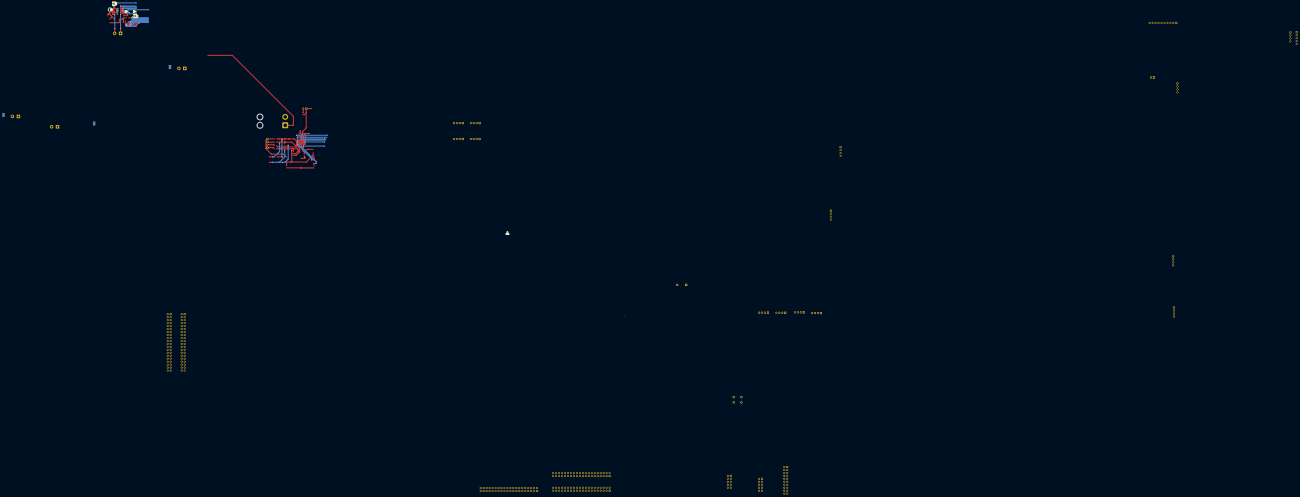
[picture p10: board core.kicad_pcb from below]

Board: 4 copper layers, 281 parts (6 on the bottom side), 318 nets.

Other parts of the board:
TP_BATT+1: TestPoint; TestPoint_Pad_D1.0mm

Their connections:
+BATT: TP_BATT+1.1; also elsewhere on the board

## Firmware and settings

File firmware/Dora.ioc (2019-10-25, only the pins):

Mcu.UserName=STM32F469IITx
PA0/WKUP.Signal=ADCx_IN0
PA1.Signal=S_TIM2_CH2
PA10.Signal=USART1_RX
PA13.Signal=SYS_JTMS-SWDIO
PA14.Signal=SYS_JTCK-SWCLK
PA15.Signal=SYS_JTDI
PA2.Signal=ADCx_IN2
PA3.Signal=ADCx_IN3
PA4.Signal=DCMI_HSYNC
PA5.Signal=S_TIM2_CH1_ETR
PA6.Signal=DCMI_PIXCLK
PA7.Signal=ADCx_IN7
PA9.Signal=USART1_TX
PB0.Signal=ADCx_IN8
PB1.Signal=ADCx_IN9
PB10.Signal=S_TIM2_CH3
PB11.Signal=S_TIM2_CH4
PB13.Signal=SPI2_SCK
PB14.Signal=SPI2_MISO
PB15.Signal=SPI2_MOSI
PB2/BOOT1.GPIO_Label=Motor2_IMODE
PB2/BOOT1.Signal=GPIO_Output
PB3.Signal=SYS_JTDO-SWO
PB4.Signal=SYS_JTRST
PB6.Signal=I2C1_SCL
PB7.Signal=I2C1_SDA
PB8.Signal=DCMI_D6
PB9.Signal=DCMI_D7
PC0.Signal=ADCx_IN10
PC1.Signal=ADCx_IN11
PC14/OSC32_IN.Signal=RCC_OSC32_IN
PC15/OSC32_OUT.Signal=RCC_OSC32_OUT
PC2.Signal=ADCx_IN12
PC3.Signal=ADCx_IN13
PC4.Signal=ADCx_IN14
PC5.Signal=ADCx_IN15
PC6.Signal=DCMI_D0
PC7.Signal=DCMI_D1
PC8.Signal=DCMI_D2
PC9.Signal=DCMI_D3
PD10.GPIO_Label=D2_DigiPot_WLAT
PD10.Signal=GPIO_Output
PD11.GPIO_Label=D2_DigiPot_SHDN
PD11.Signal=GPIO_Output
PD3.Signal=DCMI_D5
PD8.GPIO_Label=D1_DigiPot_WLAT
PD8.Signal=GPIO_Output
PD9.GPIO_Label=D1_DigiPot_SHDN
PD9.Signal=GPIO_Output
PE11.Signal=S_TIM1_CH2
PE13.Signal=S_TIM1_CH3
PE14.Signal=S_TIM1_CH4
PE4.Signal=DCMI_D4
PE5.Signal=S_TIM9_CH1
PE6.Signal=S_TIM9_CH2
PE7.GPIO_Label=Motor1_nFAULT
PE7.Signal=GPIO_Input
PE8.GPIO_Label=Motor1_IMODE
PE8.Signal=GPIO_Output
PE9.Signal=S_TIM1_CH1
PF0.Signal=I2C2_SDA
PF1.Signal=I2C2_SCL
PF10.GPIO_Label=Driver_Current_Limit_CS2
PF10.Signal=GPIO_Output
PF11.GPIO_Label=Motor2_nSLEEP
PF11.Signal=GPIO_Output
PF12.GPIO_Label=Motor2_PMODE
PF12.Signal=GPIO_Output
PF13.GPIO_Label=Motor2_nFAULT
PF13.Signal=GPIO_Input
PF14.GPIO_Label=Motor1_nSLEEP
PF14.Signal=GPIO_Output
PF15.GPIO_Label=Motor1_PMODE
PF15.Signal=GPIO_Output
PF2.Signal=GPIO_Input
PF3.Signal=GPIO_Input
PF4.Signal=GPIO_Input
PF5.Signal=GPIO_Input
PF6.Signal=S_TIM10_CH1
PF7.Signal=GPIO_Input
PF8.Signal=GPIO_Input
PF9.GPIO_Label=Driver_Current_Limit_CS1
PF9.Signal=GPIO_Output
PG0.GPIO_Label=Rotary_SW
PG0.Signal=GPIO_Input
PG1.GPIO_Label=Rotary_CLK
PG1.Signal=GPIO_Input
PG10.GPIO_Label=IR_SEL0
PG10.Signal=GPIO_Output
PG11.GPIO_Label=IR_SEL1
PG11.Signal=GPIO_Output
PG12.GPIO_Label=IR_SEL2
PG12.Signal=GPIO_Output
PG13.GPIO_Label=WP
PG13.Signal=GPIO_Output
PG14.GPIO_Label=Battery_Overcurrent
PG14.Signal=GPIO_Input
PG2.GPIO_Label=Rotary_DT
PG2.Signal=GPIO_Input
PG3.GPIO_Label=LEFT_ENC1
PG3.Signal=GPIO_Input
PG4.GPIO_Label=LEFT_ENC2
PG4.Signal=GPIO_Input
PG5.GPIO_Label=RIGHT_ENC1
PG5.Signal=GPIO_Input
PG6.GPIO_Label=RIGHT_ENC2
PG6.Signal=GPIO_Input
PG9.Signal=DCMI_VSYNC
PH0/OSC_IN.Signal=RCC_OSC_IN
PH1/OSC_OUT.Signal=RCC_OSC_OUT
PH2.GPIO_Label=OLED_EN
PH2.Signal=GPIO_Output
PH3.GPIO_Label=Ultra_EN
PH3.Signal=GPIO_Output
PH4.GPIO_Label=IR_EN
PH4.Signal=GPIO_Output
PH5.GPIO_Label=RPi_EN
PH5.Signal=GPIO_Output
PH6.GPIO_Label=Camera_EN
PH6.Signal=GPIO_Output
PH7.GPIO_Label=LoRa_EN
PH7.Signal=GPIO_Output
PI0.GPIO_Label=Ultra1_TRIG
PI0.Signal=GPIO_Output
PI1.GPIO_Label=Ultra1_ECHO
PI1.Signal=GPIO_Input
PI3.GPIO_Label=Ultra2_TRIG
PI3.Signal=GPIO_Output
PI4.GPIO_Label=Ultra2_ECHO
PI4.Signal=GPIO_Input
PI5.GPIO_Label=Ultra3_TRIG
PI5.Signal=GPIO_Output
PI6.GPIO_Label=Ultra3_ECHO
PI6.Signal=GPIO_Input
PI7.GPIO_Label=Ultra4_TRIG
PI7.Signal=GPIO_Output
PI8.GPIO_Label=Ultra4_ECHO
PI8.Signal=GPIO_Input

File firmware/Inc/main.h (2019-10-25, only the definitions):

#define Ultra4_ECHO_Pin GPIO_PIN_8
#define Ultra4_ECHO_GPIO_Port GPIOI
#define Driver_Current_Limit_CS1_Pin GPIO_PIN_9
#define Driver_Current_Limit_CS1_GPIO_Port GPIOF
#define Driver_Current_Limit_CS2_Pin GPIO_PIN_10
#define Driver_Current_Limit_CS2_GPIO_Port GPIOF
#define OLED_EN_Pin GPIO_PIN_2
#define OLED_EN_GPIO_Port GPIOH
#define Ultra_EN_Pin GPIO_PIN_3
#define Ultra_EN_GPIO_Port GPIOH
#define IR_EN_Pin GPIO_PIN_4
#define IR_EN_GPIO_Port GPIOH
#define RPi_EN_Pin GPIO_PIN_5
#define RPi_EN_GPIO_Port GPIOH
#define Motor2_IMODE_Pin GPIO_PIN_2
#define Motor2_IMODE_GPIO_Port GPIOB
#define Motor2_nSLEEP_Pin GPIO_PIN_11
#define Motor2_nSLEEP_GPIO_Port GPIOF
#define Motor2_PMODE_Pin GPIO_PIN_12
#define Motor2_PMODE_GPIO_Port GPIOF
#define Motor2_nFAULT_Pin GPIO_PIN_13
#define Motor2_nFAULT_GPIO_Port GPIOF
#define Motor1_nSLEEP_Pin GPIO_PIN_14
#define Motor1_nSLEEP_GPIO_Port GPIOF
#define Motor1_PMODE_Pin GPIO_PIN_15
#define Motor1_PMODE_GPIO_Port GPIOF
#define Rotary_SW_Pin GPIO_PIN_0
#define Rotary_SW_GPIO_Port GPIOG
#define Rotary_CLK_Pin GPIO_PIN_1
#define Rotary_CLK_GPIO_Port GPIOG
#define Motor1_nFAULT_Pin GPIO_PIN_7
#define Motor1_nFAULT_GPIO_Port GPIOE
#define Motor1_IMODE_Pin GPIO_PIN_8
#define Motor1_IMODE_GPIO_Port GPIOE
#define Camera_EN_Pin GPIO_PIN_6
#define Camera_EN_GPIO_Port GPIOH
#define LoRa_EN_Pin GPIO_PIN_7
#define LoRa_EN_GPIO_Port GPIOH
#define D1_DigiPot_WLAT_Pin GPIO_PIN_8
#define D1_DigiPot_WLAT_GPIO_Port GPIOD
#define D1_DigiPot_SHDN_Pin GPIO_PIN_9
#define D1_DigiPot_SHDN_GPIO_Port GPIOD
#define D2_DigiPot_WLAT_Pin GPIO_PIN_10
#define D2_DigiPot_WLAT_GPIO_Port GPIOD
#define D2_DigiPot_SHDN_Pin GPIO_PIN_11
#define D2_DigiPot_SHDN_GPIO_Port GPIOD
#define Rotary_DT_Pin GPIO_PIN_2
#define Rotary_DT_GPIO_Port GPIOG
#define LEFT_ENC1_Pin GPIO_PIN_3
#define LEFT_ENC1_GPIO_Port GPIOG
#define LEFT_ENC2_Pin GPIO_PIN_4
#define LEFT_ENC2_GPIO_Port GPIOG
#define RIGHT_ENC1_Pin GPIO_PIN_5
#define RIGHT_ENC1_GPIO_Port GPIOG
#define RIGHT_ENC2_Pin GPIO_PIN_6
#define RIGHT_ENC2_GPIO_Port GPIOG
#define Ultra1_TRIG_Pin GPIO_PIN_0
#define Ultra1_TRIG_GPIO_Port GPIOI
#define Ultra1_ECHO_Pin GPIO_PIN_1
#define Ultra1_ECHO_GPIO_Port GPIOI
#define Ultra2_TRIG_Pin GPIO_PIN_3
#define Ultra2_TRIG_GPIO_Port GPIOI
#define IR_SEL0_Pin GPIO_PIN_10
#define IR_SEL0_GPIO_Port GPIOG
#define IR_SEL1_Pin GPIO_PIN_11
#define IR_SEL1_GPIO_Port GPIOG
#define IR_SEL2_Pin GPIO_PIN_12
#define IR_SEL2_GPIO_Port GPIOG
#define WP_Pin GPIO_PIN_13
#define WP_GPIO_Port GPIOG
#define Battery_Overcurrent_Pin GPIO_PIN_14
#define Battery_Overcurrent_GPIO_Port GPIOG
#define Ultra2_ECHO_Pin GPIO_PIN_4
#define Ultra2_ECHO_GPIO_Port GPIOI
#define Ultra3_TRIG_Pin GPIO_PIN_5
#define Ultra3_TRIG_GPIO_Port GPIOI
#define Ultra3_ECHO_Pin GPIO_PIN_6
#define Ultra3_ECHO_GPIO_Port GPIOI
#define Ultra4_TRIG_Pin GPIO_PIN_7
#define Ultra4_TRIG_GPIO_Port GPIOI

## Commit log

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2019-06-20 [PCB] MCU Decoupling Capacitors
    [mcu.sch, rasbot.sch]
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2019-06-20 [PCB & Firmware] SWD Interface
    [mcu.sch, rasbot.sch]
2019-06-20 [PCB] Reset Button, Power LED, BOOT pins and LSE Crystal
    [mcu.sch]
2019-06-20 [PCB] Crystal Capacitor Sizing
    [mcu.sch]
2019-06-20 [PCB & Firmware] SWD Connector and Reset Button Footprint and Firmware LSE Enable
    [mcu.sch]
2019-06-20 [PCB] Connect LSE to MCU
    [mcu.sch]
2019-06-20 [PCB & Firmware] Motors PWM Signal MCU Pins
    [mcu.sch, rasbot.sch]
2019-06-20 [PCB & Firmware] Line Sensors MCU Pins
    [mcu.sch, rasbot.sch]
2019-06-20 [PCB & Firmware] I2C for LCD SSD1306 MCU Pins
    [mcu.sch, rasbot.sch]
2019-06-20 [PCB & Firmware] Light Sensor MCU Pin
    [mcu.sch, rasbot.sch]
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2019-07-07 Infrared index starts at 0
    [infrared.sch, infrared_matrix.sch, mcu.sch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]
2019-07-09 Use Buses for IR sensors
    [infrared.sch, infrared_matrix.sch, ir.sch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]
2019-07-22 IR matrix complete minus control transistor
    [infrared.sch, infrared_matrix.sch, infrared_row.sch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]
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2019-07-22 IR Matrix - Missing Supply Connection
    [infrared_row.sch, ir.sch, mcu.sch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]
2019-07-24 Resistor value corrected
    [infrared_row.sch, ir.sch, mcu.sch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]
2019-07-25 Added 0 ohm resistor to power switch
    [ir.sch]
2019-07-25 Buzzer and RGB LED interfaces
    [infrared_row.sch, interfaces.sch, ir.sch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]
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2019-07-28 Connect IR Matrix to MCU
    [infrared_row.sch, ir.sch, mcu.sch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]
2019-07-28 Optimized IR MCU pins
    [infrared_row.sch, mcu.sch]
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2019-07-28 Fix IR Sensors
    [infrared_row.sch, ir.sch]
2019-07-28 Fix resistor IR Matrix
    [infrared_row.sch, ir.sch]
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2019-07-28 Fix Merges
    [infrared_row.sch, interfaces.sch, ir.sch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]
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2019-07-28 Fix and Anotate design
    [infrared_row.sch, interfaces.sch, ir.sch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]
2019-07-28 MCU connections, OLED and Sonar
    [infrared_row.sch, interfaces.sch, ir.sch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]
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2019-07-29 Fix pins
    [mcu.sch]
2019-07-29 Battery monitor .sch early commit. Not yet included in hierarchical sheet
    [power.sch]
2019-07-29 Moved Power inside the project
    [infrared_row.sch, interfaces.sch, ir.sch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]
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2019-07-30 Cell voltage, BATT+, current sensor and VCTL changed. Changes to lib changed the other .sch
    [infrared_row.sch, interfaces.sch, ir.sch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]
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2019-08-05 Project divided into Core and Plugins
    [core.kicad_pcb, core.sch, infrared_row.sch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]
2019-08-14 Add 256kB EEPROM to the project
    [core.sch, interfaces.sch, mcu.sch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]
2019-08-14 Add pull-up resistor to the SDA line
    [mcu.sch]
2019-08-14 pull-up resistor on SCL and WP
    According to Application note AN1028 WP can't be left floating and both I2C pins and WP should have a pull-up
    [mcu.sch]
2019-08-14 Decoupling cap as AN1028 suggests
    [mcu.sch]
2019-08-14 Tidy up
    Moved around circuit blocks
    [mcu.sch]
2019-08-14 Changed WP pull up to 10K Ohms to reduce power draw
    [mcu.sch]
2019-08-14 A0 and A1 are not connected according to datasheet
    [mcu.sch]
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2019-08-14 Fixes all around
    [interfaces.sch, mcu.sch, power.sch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]
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2019-08-14 fix libraries and annotate schematic
    [core.sch, driver.sch, interfaces.sch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]
2019-08-15 Fix libraries
    [interfaces.sch]
2019-08-16 Preliminary circuitry for the DRV8876 motor driver
    [core.sch, driver.sch, interfaces.sch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]
2019-08-16 Add connection from PAD to GND
    [driver.sch]
2019-08-16 Add missing transistor to sensor sheet
    [driver.sch, sensors.sch]
2019-08-17 Add current limiting resistor and bulk capacitor
    [driver.sch]
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2019-08-21 Prettify Motor Driver Schematic
    [driver.sch]
2019-08-21 Add RPi connectors and fix tons of bugs
    [core.sch, driver.sch, interfaces.sch]
2019-08-21 Complete circuit of the available Logitech USB mouse
    [mouse usb.kicad_pcb, mouse usb.sch]
2019-08-21 Partial circuit of the HP PS/2 mouse
    [mouse ps2.kicad_pcb, mouse ps2.sch]
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2019-08-21 Size SEPIC inductor and MOSFETs
    [buck.sch]
2019-08-21 Fix division in power
    [batmon.sch, buck.sch, core.sch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]
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2019-08-21 redid NTC connection to the BMS and changed current sense resistors
    [batmon.sch, buck.sch, core.sch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]
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2019-08-21 Fix connection to Vin
    [batmon.sch, buck.sch, core.sch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]
2019-08-21 Fix Library
    [batmon.sch, buck.sch, core.sch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]
2019-08-21 Fix Driver
    [driver.sch]
2019-08-24 Give Up SEPIC and 9V LDO design
    [batmon.sch, buck.sch, infrared_row.sch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]
2019-08-24 Designed 5V and 3.3V (MCU) LDOs
    [core.sch, driver.sch, interfaces.sch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]
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2019-08-25 Fix merge problems
    [comms.sch, core.sch, driver.sch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]
2019-08-26 Updated Driver to DRV8874-Q1
    [driver.sch]
2019-08-26 STM32F469IIT6 in schematic and firmware init
    [core.sch, mcu.sch]
2019-08-28 Tune crystals loading capacitance
    [core.kicad_pcb, mcu.sch]
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2019-08-30 Fix RPI
    [interfaces.sch]
2019-08-30 added camera and core MCU pins
    [core.sch, driver.sch, interfaces.sch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]
2019-08-31 Added camera, Motor driver PWM, RGB LEDs
    [mcu.sch]
2019-08-31 Connected LoRa and OLED
    [core.sch, mcu.sch]
2019-08-31 Fix LED footprint
    [mcu.sch]
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2019-09-08 IR merged with core
    [comms.sch, core.sch, driver.sch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]
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2019-09-09 Missing Footprints
    [infrared_row.sch, power.sch]
2019-09-16 Fix camera shutdown bug
    [interfaces.sch, sensors.sch]
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2019-10-10 Pull up for overcurrent output and more protection diode
    [interfaces.sch, power.sch]
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2019-10-10 Fix Driver Connections
    [core.sch, interfaces.sch, mcu.sch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]
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2019-10-12 tidy up power sheet
    [power.sch]
2019-10-19 3.3 - 5V level shifter sonar with 2n3904
    [comms.sch, sensors.sch]
2019-10-21 add probe points in sonar
    [sensors.sch]
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2019-10-25 Added DigiPot to the Drivers for current limit control
    [core.sch, driver.sch, motors.sch]
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2019-10-25 Connect WLAT and SHDN
    [core.sch, driver.sch, mcu.sch]
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2021-03-02 Updated ultrassonic level shifter
    [comms.sch, core.sch, driver.sch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]
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2021-03-02 Removed ghost pin and change SDA to Bidirectional
    [core.sch, infrared_row.sch, interfaces.sch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]
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2021-03-02 Fix all ERC errors
    [IR_board.sch, infrared_row.sch]
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2021-03-02 Fix errors and JTAG connectors
    [comms.sch, driver.sch, mcu.sch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]
2021-03-02 Fix bug in BMS connections
    [driver.sch, mcu.sch, power.sch]
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2021-03-02 Replace MCU with more pin variant
    [mcu.sch]
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2021-03-02 Changed RPi Buck to new model in order to support Jetson Nano boards
    Fixed a bug in the Ultrassonic sensors level-shifters
    [comms.sch, core.sch, driver.sch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]
2021-03-02 revert changes to Level-shifters. Optimize for single-direction operation
    [power.sch, ultrasonic.sch]
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2021-03-02 Minor BMS revision and added bulk capacitor footprints
    [core.sch, driver.sch, mcu.sch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]
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2021-03-07 Added buck to IR_board - Same as Main board buck. Added footprint for 12AWG wire connector (XT60) - need to check size of the wire
    [IR_board.sch, infrared_row.sch]
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2021-05-13 MCP41HV51 symbol - SDO changed from output to tri-state
    [driver.sch, mcu.sch, motors.sch]
2021-05-13 Added TVS diode and missing footprints
    [IR_board.sch, driver.sch, infrared_row.sch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]
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2021-07-06 Updated doc and reorganization of components in main board layout
    [core.kicad_pcb]
2021-07-12 Changes to schematic. QOL changes to I2C TPs
    [driver.sch, mcu.sch, motors.sch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]
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

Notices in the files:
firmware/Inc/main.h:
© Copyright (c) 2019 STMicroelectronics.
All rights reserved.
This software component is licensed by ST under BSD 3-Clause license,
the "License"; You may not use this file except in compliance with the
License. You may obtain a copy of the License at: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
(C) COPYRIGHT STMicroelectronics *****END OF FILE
